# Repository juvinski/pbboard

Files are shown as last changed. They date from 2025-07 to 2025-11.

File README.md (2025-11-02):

# PocketBeagle 2 DIY Cape for Ardupilot
This project aim enable to run [Ardupilot](https://ardupilot.org/) on the [PocketBeagle 2](https://www.beagleboard.org/boards/pocketbeagle-2) Board.

# Board manufacturing
## PCBWay
I'm using the PCBWay to produce the boards - 5 boards have a cost of USD 5.00
You can use [this file](Board_Archives_Manufacturing/PocketPilot2.kicad_pcb.zip).

## Other Services
I believe the same file can be used by other online PCB manufactures.

# Board Images
## Board Only
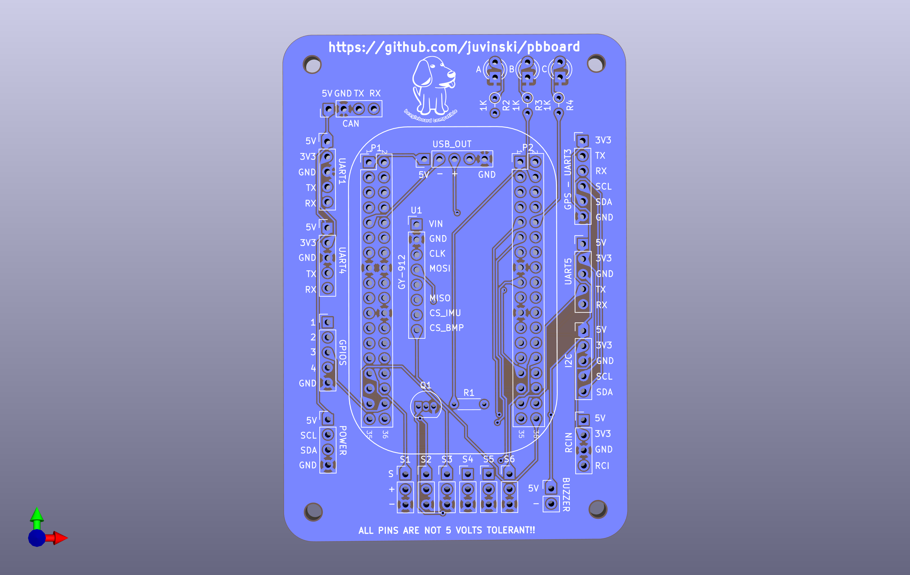
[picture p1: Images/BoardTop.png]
BOARD ONLY


## Board Components - Preview
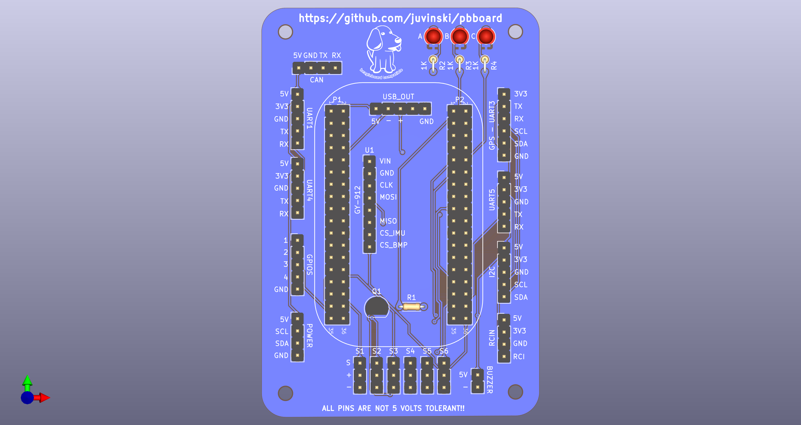
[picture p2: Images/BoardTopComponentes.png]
BOARD_PARTS


# Hardware instructions
## Board manufacturing
### Board version 1.1
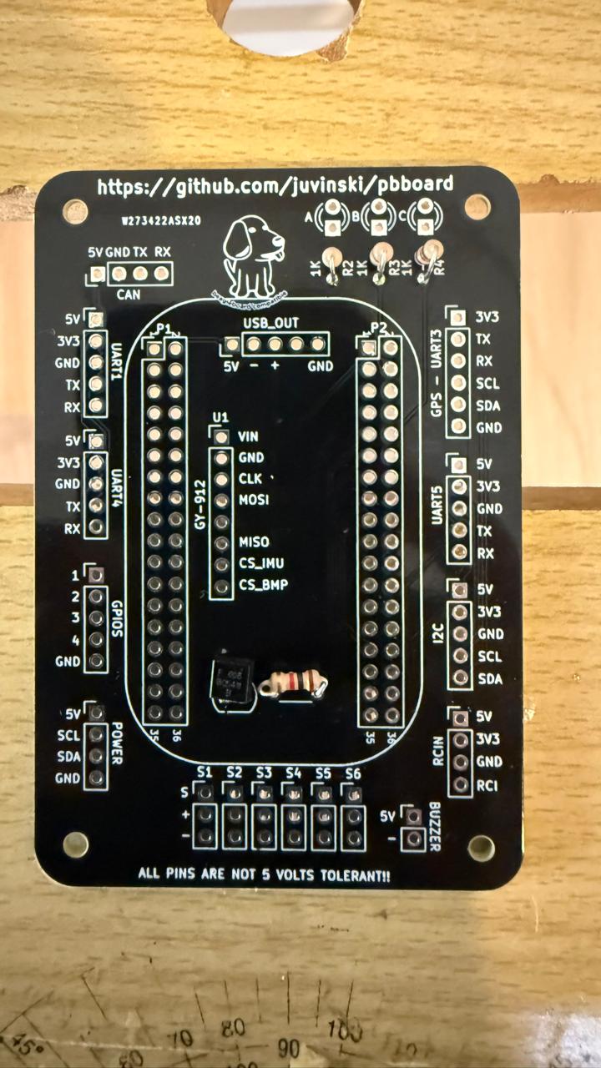
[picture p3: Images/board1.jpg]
Board manufacturing

### Soldering resistors, transistor and rc output headers 
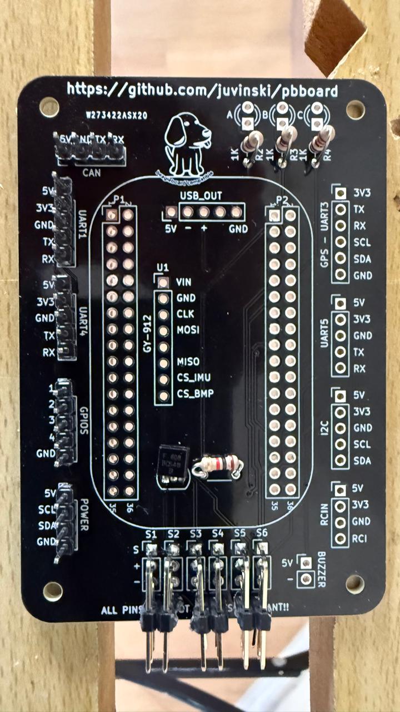
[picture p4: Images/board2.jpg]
Board manufacturing

### Soldering output headers 
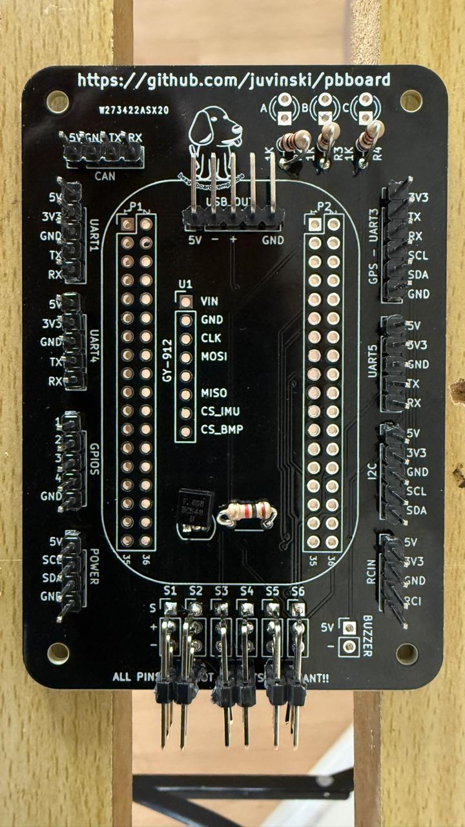
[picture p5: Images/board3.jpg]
Board manufacturing

### Soldering Pocketbeagle 2 headers
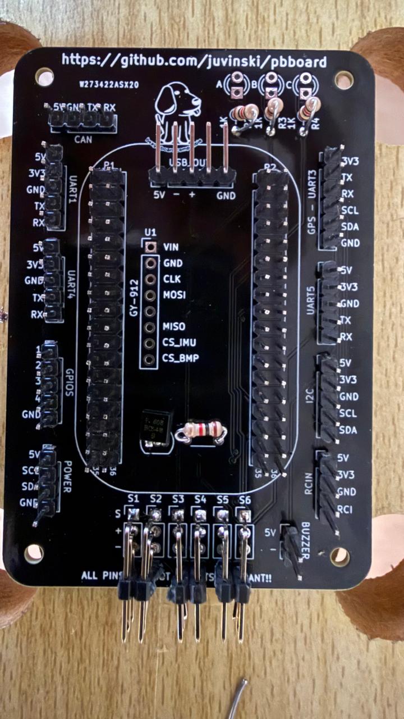
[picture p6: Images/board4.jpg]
Board manufacturing

### Soldering Leds
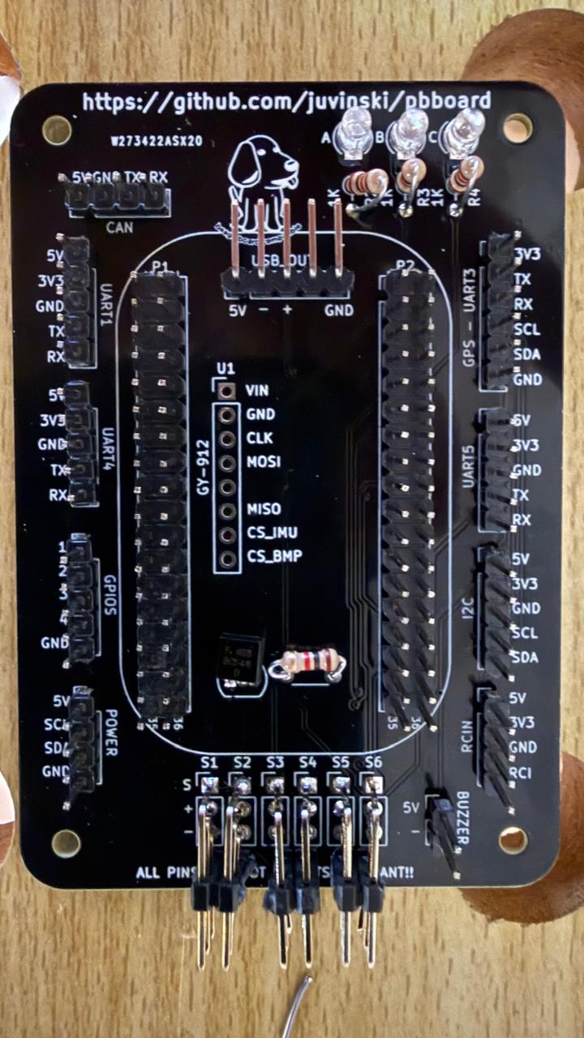
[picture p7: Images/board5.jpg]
Board manufacturing

### Preparing the IMU - using double sided tape
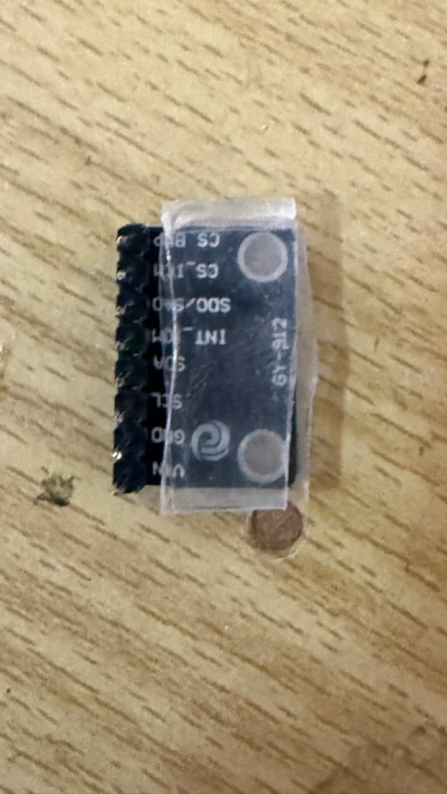
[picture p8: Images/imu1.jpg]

### Soldering the IMU
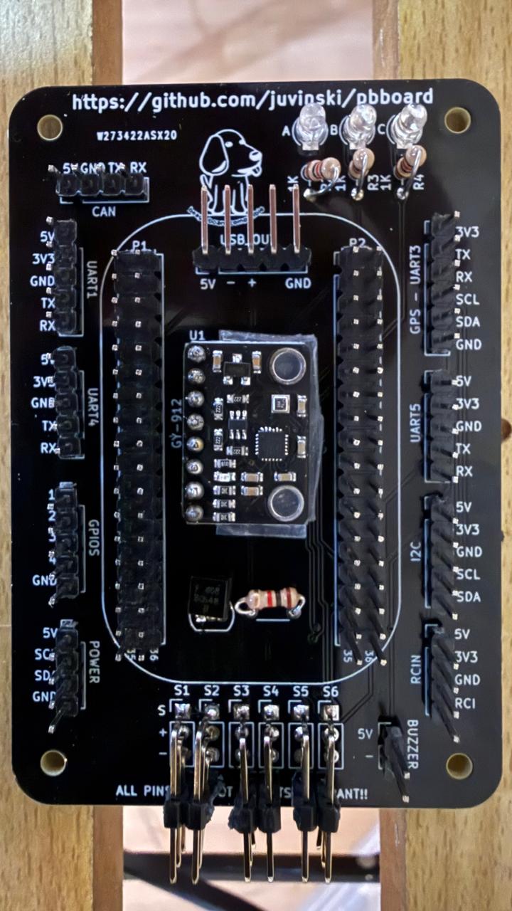
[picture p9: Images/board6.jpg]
Board manufacturing

### Finished
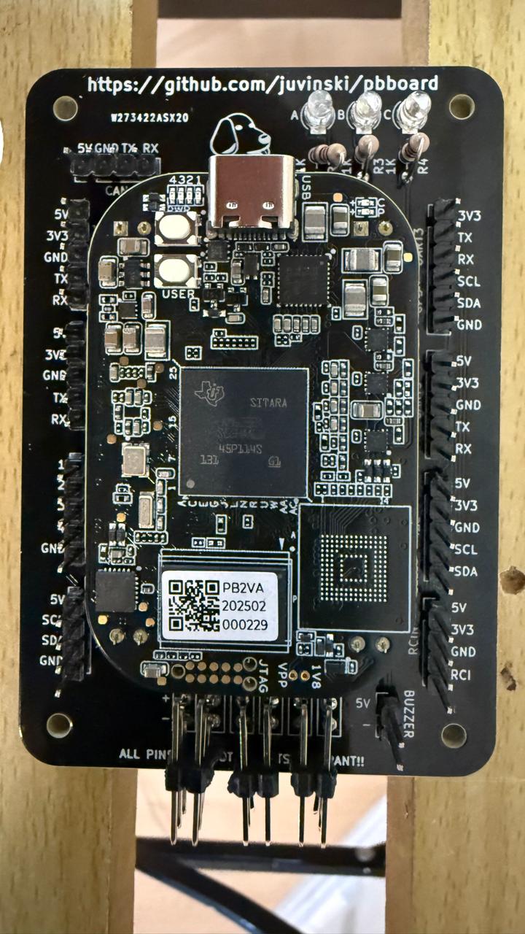
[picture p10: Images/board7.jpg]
Board manufacturing


## Schematic
The schematic can be found [here](Schematic/PocketPilot2.pdf).

## Parts
	- 1 IMU [GY-912](https://www.ebay.com/itm/166809278501)
	- 4 Resistors 1KΩ
	- 2 Resistors 10k 0.1%
	- 2 Resistors 20k 0.1%
	- 3 Led Red, Blue and Green color 
	- 1 BC548 NPN Transistor
	- 1 I2C Digital [Power Module/Monitor](https://ardupilot.org/copter/docs/common-powermodule-landingpage.html#i2c-power-monitor)
	- 6 Pin header 1 x 5 straight
	- 3 Pin header 1 x 4 straight
	- 1 Pin header 1 x 6 straight
	- 6 Pin header 1 x 3 straight or 90°
	- 1 Pin header 1 x 2 straight
	- 1 Pin header female 1 x 8 - optional

## Details
To use the I2C power sensing you can use the [Holybro PM2D](https://holybro.com/products/pm02d-power-module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).
The analog power sensing is using 4 resistors.
The outputs of the sensor was changed by a female reader and both 5Volts output connectec together as the GND.
The GY-912 is soldered direct over the board once the PocketBeagle 2 is over it and the space between the PocketBeagle 2 board and the DIY board it's small.
Once the Kicad project is shared, you can modify freely according your needs.
The CAN interface need a CAN Transceiver breadboard like CJMCU-1051 (or any TJA1051) with 3.3Volts interface for TX and RX.
The buzzer circuit is simple but powerfull.
For the USB OTG you are free to use what kind of USB is more suitable for you. The board export 5 pins there the 4th is not connected.

## Board details
	- 4 UARTs - One have the I2C to be used with a GPS + Compass
 	- 3 I2Cs - One is under the Power header, Other in the GPS header and one for I2C
  	- 4 GPIO pins with GND
	- Support for I2C and/or Power Sensing
   	- 6 Outputs
   	- Buzzer output for an Active buzzer
*** All pins is just 3.3 Volts ***  
*** 5 Volts will brick your PocketBeagle 2 ***

# Software Instructions
The software instructions can be found at [Ardupilot Wiki] (https://github.com/juvinski/ardupilot_wiki/blob/pocket2/common/source/docs/common-pocketbeagle-2.rst).
This version will be present in Ardupilot official wiki when the version 4.7 release.

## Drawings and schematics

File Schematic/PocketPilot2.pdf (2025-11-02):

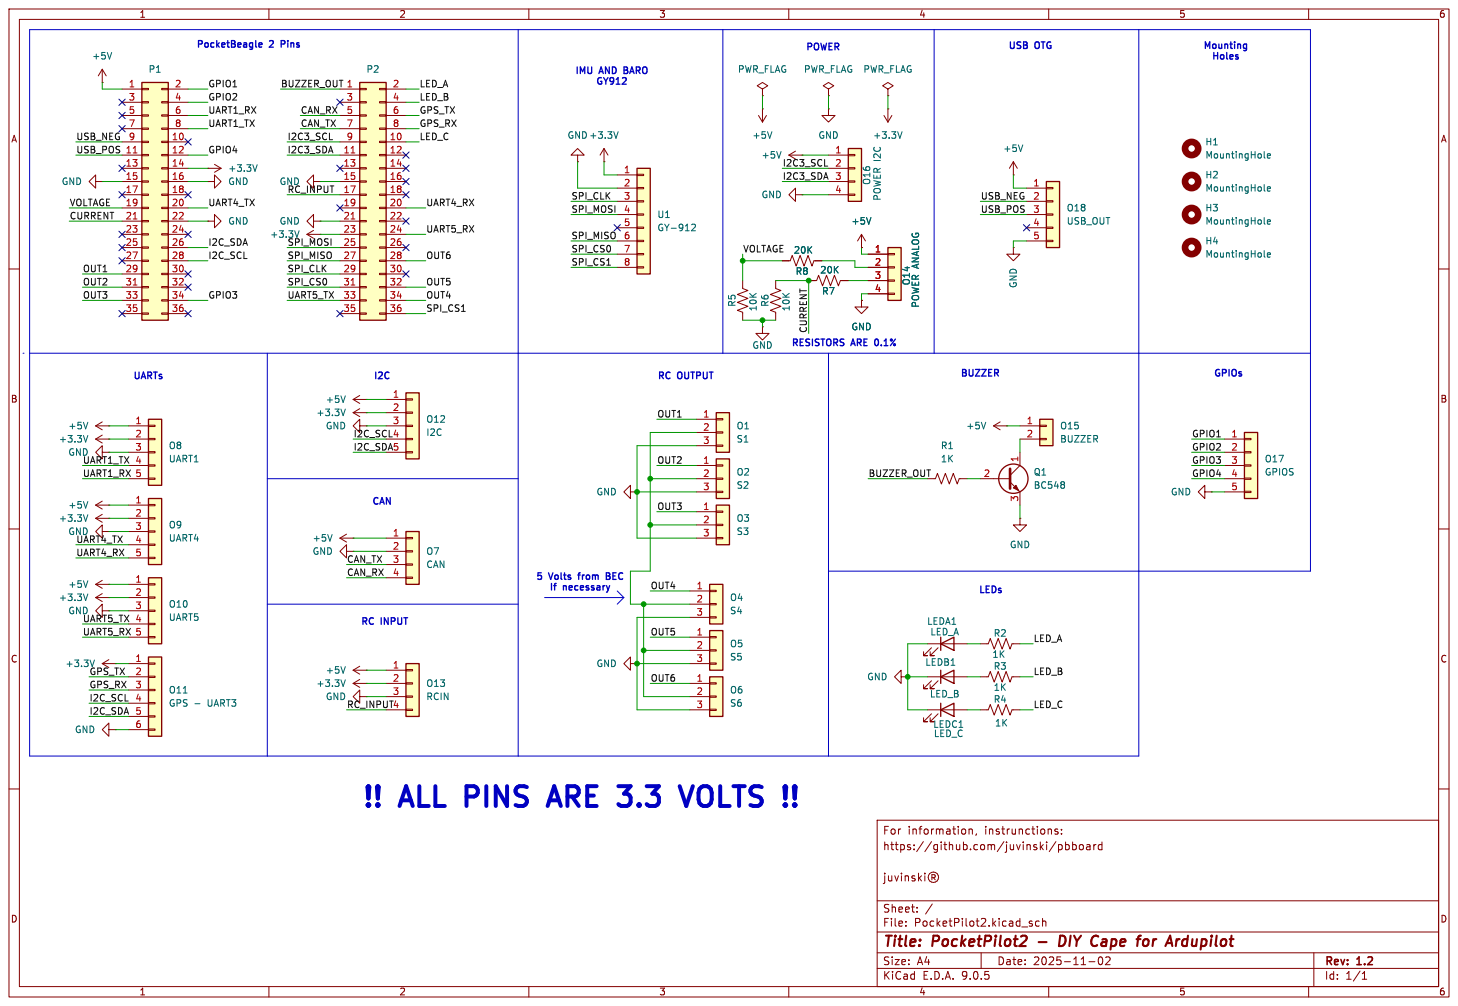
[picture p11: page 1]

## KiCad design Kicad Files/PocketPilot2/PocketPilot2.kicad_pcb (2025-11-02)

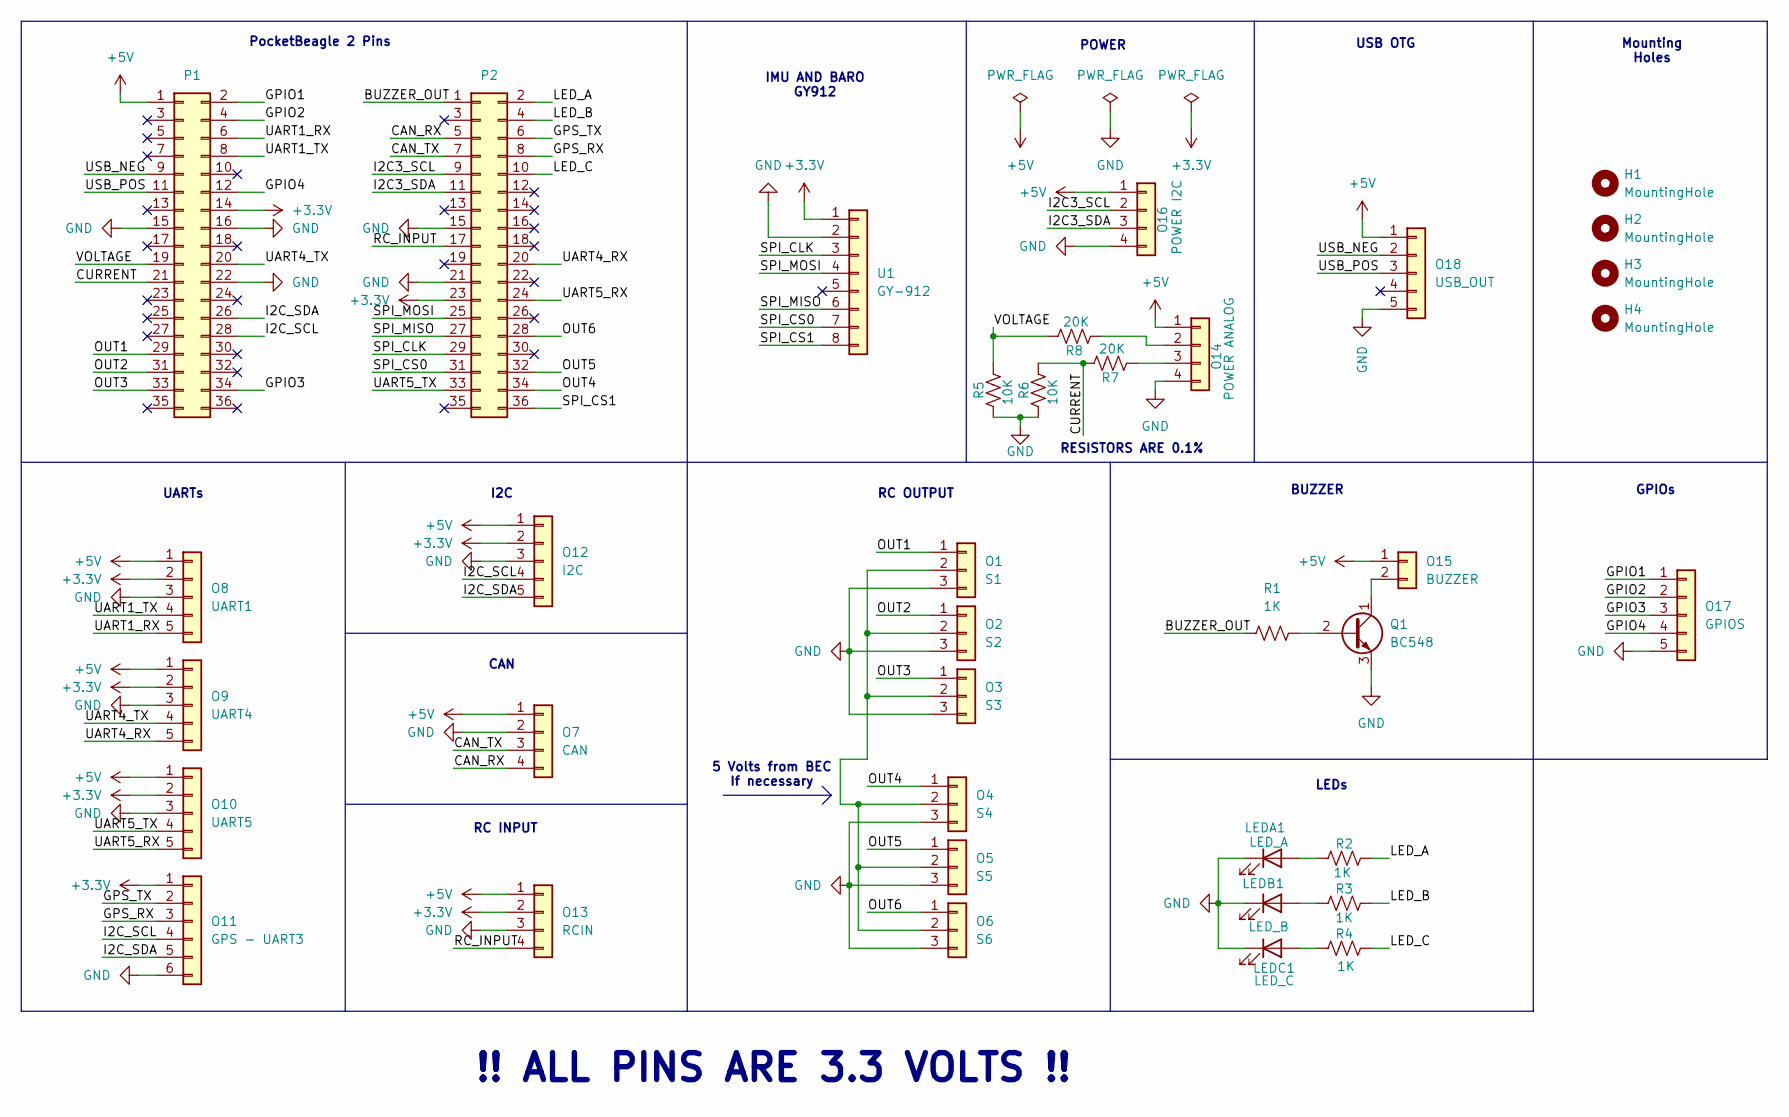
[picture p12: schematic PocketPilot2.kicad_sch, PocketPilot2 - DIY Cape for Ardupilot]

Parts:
H1, H2, H3, H4: MountingHole; MountingHole_2.7mm_M2.5
LEDA1: LED_A; LED_D3.0mm
LEDB1: LED_B; LED_D3.0mm
LEDC1: LED_C; LED_D3.0mm
O1: S1; PinHeader_1x03_P2.54mm_Vertical
O2: S2; PinHeader_1x03_P2.54mm_Vertical
O3: S3; PinHeader_1x03_P2.54mm_Vertical
O4: S4; PinHeader_1x03_P2.54mm_Vertical
O5: S5; PinHeader_1x03_P2.54mm_Vertical
O6: S6; PinHeader_1x03_P2.54mm_Vertical
O7: CAN; PinHeader_1x04_P2.54mm_Vertical
O8: UART1; PinHeader_1x05_P2.54mm_Vertical
O9: UART4; PinHeader_1x05_P2.54mm_Vertical
O10: UART5; PinHeader_1x05_P2.54mm_Vertical
O11: GPS - UART3; PinHeader_1x06_P2.54mm_Vertical
O12: I2C; PinHeader_1x05_P2.54mm_Vertical
O13: RCIN; PinHeader_1x04_P2.54mm_Vertical
O14: POWER ANALOG; PinHeader_1x04_P2.54mm_Vertical
O15: BUZZER; PinHeader_1x02_P2.54mm_Vertical
O16: POWER I2C; PinHeader_1x04_P2.54mm_Vertical
O17: GPIOS; PinHeader_1x05_P2.54mm_Vertical
O18: USB_OUT; PinHeader_1x05_P2.54mm_Vertical
P1, P2: Conn_02x18_Odd_Even; PinHeader_2x18_P2.54mm_Vertical
Q1: BC548; TO-92_Inline
R1: 1K; R_Axial_DIN0204_L3.6mm_D1.6mm_P5.08mm_Horizontal
R2, R3, R4: 1K; R_Axial_DIN0204_L3.6mm_D1.6mm_P2.54mm_Vertical
R5, R6: 10K; R_Axial_DIN0204_L3.6mm_D1.6mm_P5.08mm_Horizontal
R7, R8: 20K; R_Axial_DIN0204_L3.6mm_D1.6mm_P5.08mm_Horizontal
U1: GY-912; PinSocket_1x08_P2.54mm_Vertical

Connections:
+3.3V: O8.2, O9.2, O10.2, O11.1, O12.2, O13.2, P1.14, P2.23, U1.1
+5V: O7.1, O8.1, O9.1, O10.1, O12.1, O13.1, O14.1, O15.1, O16.1, O18.1, P1.1
/BUZZER_OUT: P2.1, R1.1
/CAN_RX: O7.4, P2.5
/CAN_TX: O7.3, P2.7
/CURRENT: P1.21, R6.2, R7.2
/GPIO1: O17.1, P1.2
/GPIO2: O17.2, P1.4
/GPIO3: O17.3, P1.34
/GPIO4: O17.4, P1.12
/GPS_RX: O11.3, P2.8
/GPS_TX: O11.2, P2.6
/I2C3_SCL: O16.2, P2.9
/I2C3_SDA: O16.3, P2.11
/I2C_SCL: O11.4, O12.4, P1.28
/I2C_SDA: O11.5, O12.5, P1.26
/LED_A: P2.2, R2.2
/LED_B: P2.4, R3.2
/LED_C: P2.10, R4.2
/OUT1: O1.1, P1.29
/OUT2: O2.1, P1.31
/OUT3: O3.1, P1.33
/OUT4: O4.1, P2.34
/OUT5: O5.1, P2.32
/OUT6: O6.1, P2.28
/RC_INPUT: O13.4, P2.17
/SPI_CLK: P2.29, U1.3
/SPI_CS0: P2.31, U1.7
/SPI_CS1: P2.36, U1.8
/SPI_MISO: P2.27, U1.6
/SPI_MOSI: P2.25, U1.4
/UART1_RX: O8.5, P1.6
/UART1_TX: O8.4, P1.8
/UART4_RX: O9.5, P2.20
/UART4_TX: O9.4, P1.20
/UART5_RX: O10.5, P2.24
/UART5_TX: O10.4, P2.33
/USB_NEG: O18.2, P1.9
/USB_POS: O18.3, P1.11
/VOLTAGE: P1.19, R5.2, R8.2
GND: LEDA1.1 (K), LEDB1.1 (K), LEDC1.1 (K), O1.3, O2.3, O3.3, O4.3, O5.3, O6.3, O7.2, O8.3, O9.3, O10.3, O11.6, O12.3, O13.3, O14.4, O16.4, O17.5, O18.5, P1.15, P1.16, P1.22, P2.15, P2.21, Q1.3 (E), R5.1, R6.1, U1.2
unnamed: LEDA1.2 (A), R2.1
unnamed: LEDB1.2 (A), R3.1
unnamed: LEDC1.2 (A), R4.1
unnamed: O1.2, O2.2, O3.2, O4.2, O5.2, O6.2
unnamed: O14.2, R8.1
unnamed: O14.3, R7.1
unnamed: O15.2, Q1.1 (C)
unnamed: Q1.2 (B), R1.2

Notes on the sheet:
RC OUTPUT
IMU AND BARO GY912
LEDs
Mounting Holes
I2C
UARTs
BUZZER
RC INPUT
POWER
5 Volts from BEC If necessary
RESISTORS ARE 0.1%
!! ALL PINS ARE 3.3 VOLTS !!
GPIOs
PocketBeagle 2 Pins
CAN
USB OTG

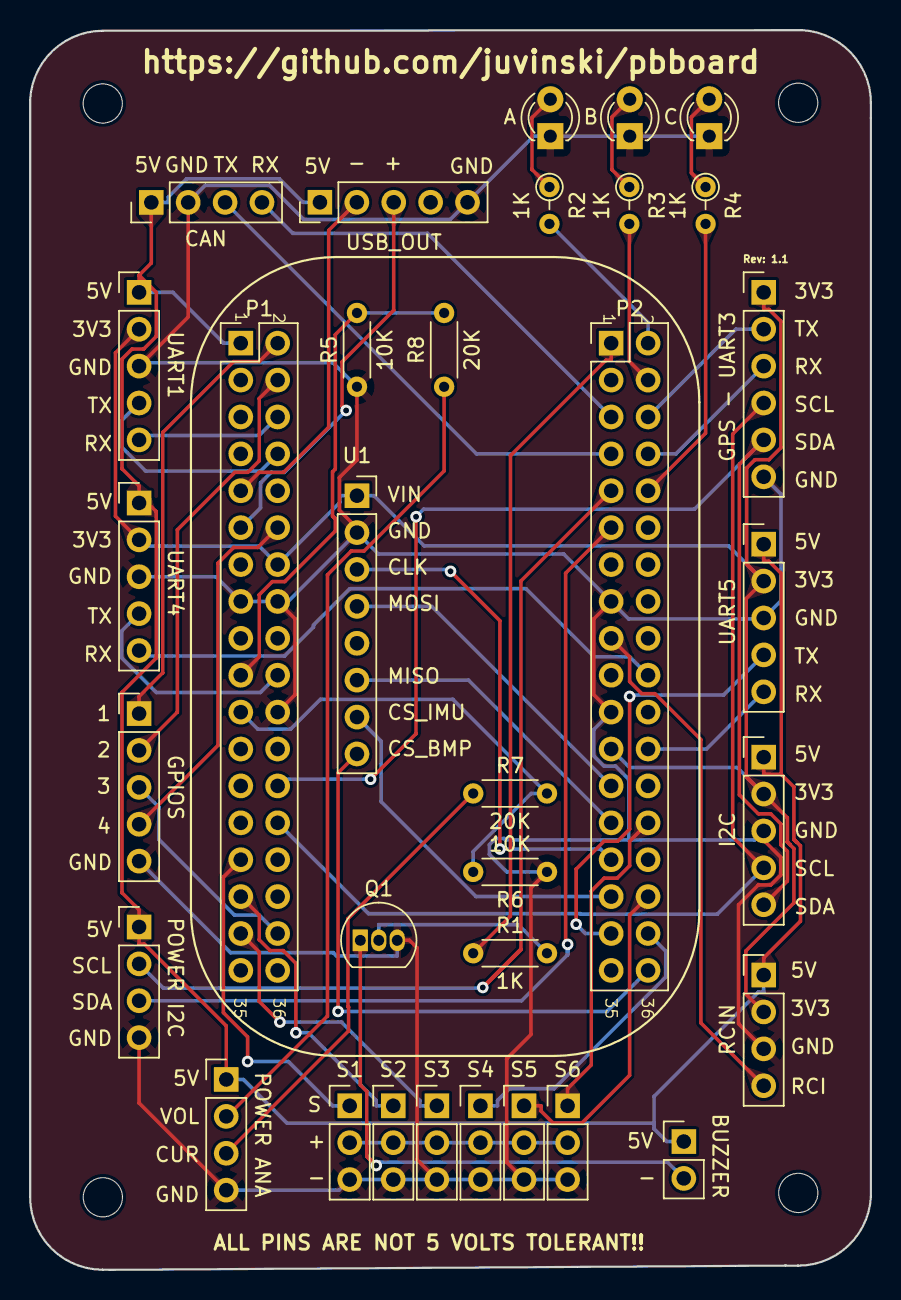
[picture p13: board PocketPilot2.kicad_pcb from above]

Board: 2 copper layers, 57.9 x 85.3 mm, 37 parts (0 on the bottom side), 49 nets.

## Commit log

2025-07-03 Commit inicial
    [PocketPilot2.dsn, PocketPilot2.kicad_pcb, PocketPilot2.kicad_sch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]
2025-07-03 Update board details
2025-07-11 Update to version to 1.1 Update GPIO pins
    [PocketPilot2.kicad_pcb, PocketPilot2.kicad_sch]
2025-11-02 Version 1.2 release Update board to add analog power sensing. Update images and instructions.
    [PocketPilot2.kicad_pcb, PocketPilot2.kicad_sch]
